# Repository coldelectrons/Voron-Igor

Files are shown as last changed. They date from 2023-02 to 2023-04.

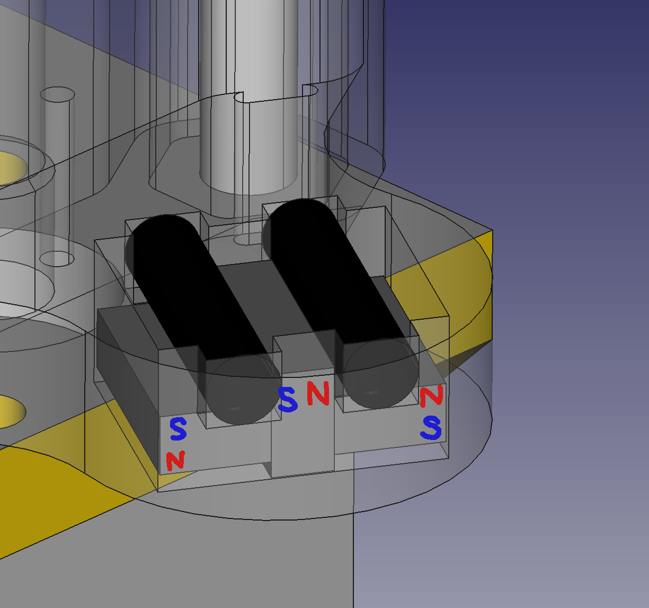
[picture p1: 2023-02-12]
pics/magnets_halbach_z_carriage.png

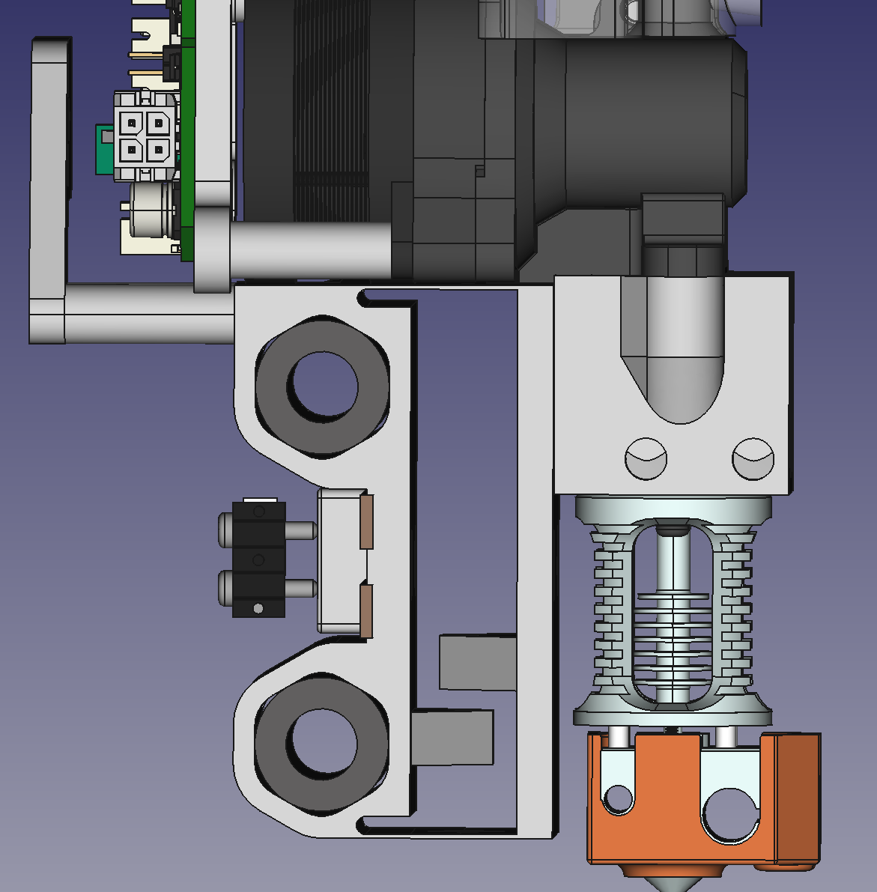
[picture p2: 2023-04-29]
pics/voron-igor-unklicky-tap-flexure.png

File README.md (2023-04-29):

# Voron Igor
It's a few good printers.

## What this is
This is my mods for a Voron Legacy.

## What did I mod?
Oh, not much.

### The tensioning idlers and motor mounts
It seems silly to come up with a good implementation and not use it simply because you
want to 'harken back' to the bad ol' days.

I have always disliked designs that tension the belts by moving the motor - and needing to
loosen/tighten 2 or more screws, relying on the motor to slide smoothly against a printed surface,
and/or needing to reach hard-to-reach places to adjust.  So I adapted the tension idlers from
the V2.4, and the motor mounts as well.

### The Y rod mounts
I elected to use some OpenBuilds 2020 extrusion I had, so it probably wasn't perfect, and the slots
were different...but the difference highlighted a design flaw in the original Legacy: The Y rods
get supported by two different datums at each end.

In the back, there is a single part that is located by the 2020 slot, and the rod spacing is fixed, and
as accurate and repeatable as the printer used to print that part.

In the front, the original idlers were a sandwich on the top and bottom of the 2020, and used pockets
to hold the rods.  Any variation the in the 2020 would mean that those rods could be not parallel.

So, I simply made a new Y rod support (x4), into which I also made a small cut so that when turned
the right direction, would allow the full travel of the gantry.

This also means that I could remove the idler tensioners, if need be, without unmounting the gantry.

### The Z axis
I found the original Legazy Z to be very...problematic. 

The rods were spaced far apart, which seemed to make rocking and binding of the whole thing to be too easy.

On top of rocking, it needed manual adjusting of the buildplate with screws. Which were on a wobbly Z axis.
That you had to touch.

This isn't 'harkening back', this is regressing.

So I adapted something like the Jubilee. I didn't know about the Voron Trident at the time, so that's what I was looking off of.

I didn't like the Jubilee's use of springs to hold down the kinematic table, because I could easily see myself
trying to lift a magnetic build plate off and stretching the springs. The springs Jubilee used were also tiny fiddly little bits.
So I came up with a solution to use magnets as effectively as possible, given what I had and could easily model.
The result is something that uses cheap magnets, in something like a Halbach array. The downside is that while I do have alot more
magnetic 'stick' than otherwise, the magnets I used are cheap, and so it's not enough to keep the table in place when I invert
the printer or turn it on it's side :)

### UnKlicky Tap?
I wanted to try making a Tap upgrade for a printer.

I'd already tried doing the KlickyNG probe, and got it working with the 'Z Calibration' hardware and Klipper module,
in order to hopefully work with any build plate I might want.

I can't say I liked it. Too much to configure, and too much that could go wrong. Naturally, when I saw the Voron Tap,
I realized I wanted something that simple - just touch the damn nozzle to the surface. Simple, right?

Right?

Because the Igor is using 8mm rods, it's not exactly stiff. Mass is a problem (always is on all printers),
and adding more wasn't an option. I also didn't want to have to source more special parts for my Igor.

I also have been wanting to try compliant mechanisms ('flexures') for a while.

Thus is born an X carriage with a flexure and a UnKlicky-esque probe switch.

Does it work? As of 20230429, I have successfully tested it for homing and probing.

## FAQ
### Why isn't this perfect
Partly because I was working on this through a couple upversions of FreeCAD, partly because I was learning more advanced
CAD as I went along, and partly because if there is one negative thing I might accuse the Voron designers of, it's CAD-wanking.

Sure, their designs work well, *and* they have a nice aesthetic, but when working from the STEP models, some things I had to
just take dimesions and start over, because of curved surfaces and such didn't let me easily mod things, or the imported STEP
would develop problems in FreeCAD when I tried to alter them.

### Why not include the full CAD files?
* My CAD files are a mess. I import other stuff, and the resulting file is HUGE.
* I use the FreeCAD-realthunder snap.
* If you open them in another FreeCAD version, they will likely break, or need a 'recompute now', at which time they will break.
* STEP files are stable

### Why the name 'Igor'?
Some people joking online saying the Legacy should have been named 'Frankenstein'
because they built it out of leftover parts. This is wrong, because Frankenstein was
the name of the *doctor*, not his creation.

I think it would be far more appropriate to adopt the name of a character from
Terry Pratchett's *Discworld* series:
 * the approach to self-improvement
 * the extreme recycling/upcycling
 * the spirit of Reprap in which one Igor can make many more
 * the way it is always just behind me when I need it

Alternative names I considered:
 * That Thing In the Cellar
 * Box O' Parts
 * Reprap Centipede

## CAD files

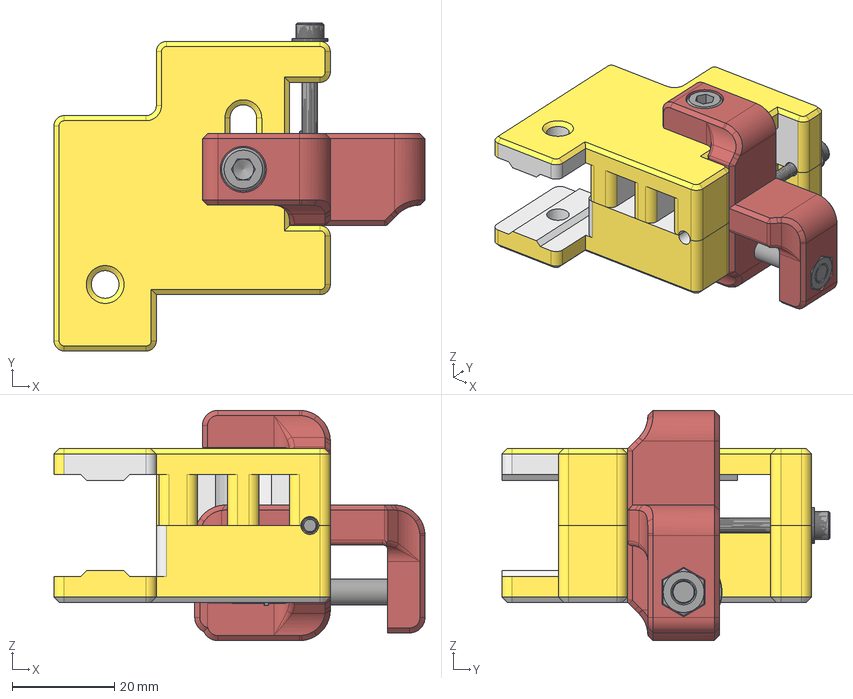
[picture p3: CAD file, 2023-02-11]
CAD/idler_A_assembly.step
72.5 x 64.1 x 45.0 mm
LCS_Origin x 6
M5x40 SHCS x 2
M5 1mm Spacer x 2
M3 Washer x 2
F695 ZZ x 2
M5 Hexnut x 2
M3 Threaded Insert (1) x 2
M3x40 SHCS x 2

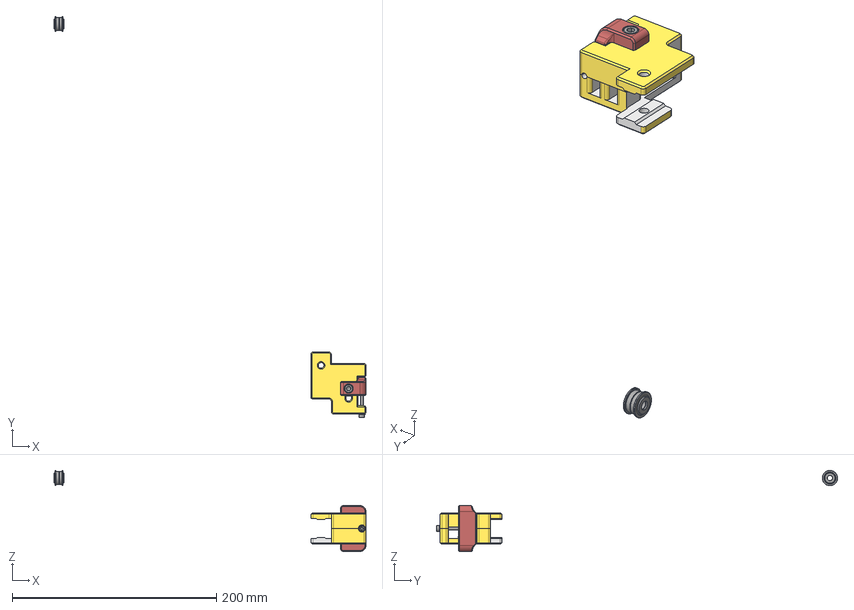
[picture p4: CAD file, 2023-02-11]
CAD/idler_B_assembly.step
305.6 x 392.9 x 79.5 mm
LCS_Origin x 6
M5x40 SHCS (1) x 2
F695 ZZ x 6
M5 1mm Spacer x 6
M5 Hexnut (1) x 2
M3x40 SHCS (1) x 2
M3 Washer x 2
M3 Threaded Insert (1) x 2

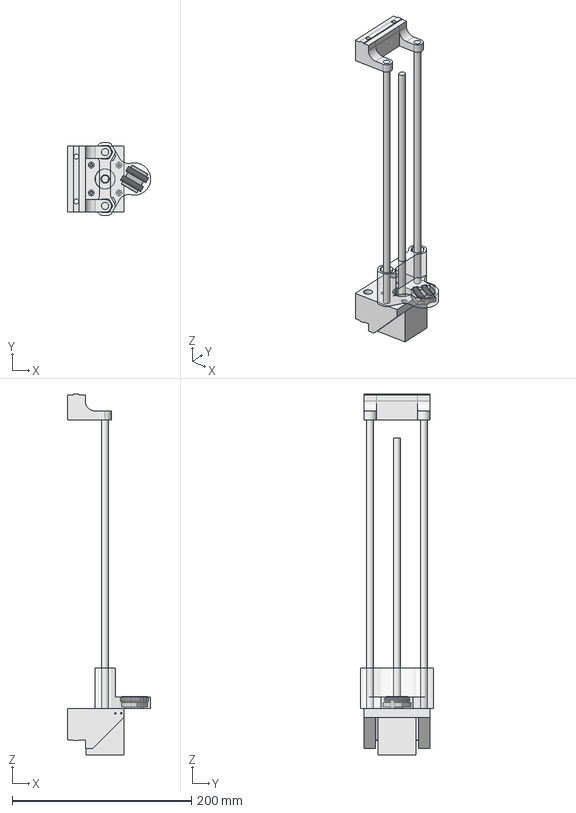
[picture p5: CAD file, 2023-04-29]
CAD/VL_configurable_z_unit.FCStd
93.0 x 81.0 x 403.0 mm
base
top
nema17_motor
leadscrew
rod1
rod2
carriage
dowels
magnets

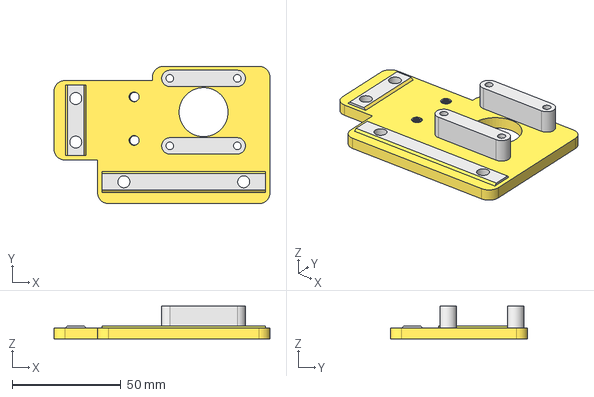
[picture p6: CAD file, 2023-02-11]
CAD/motor_A_bottom.step
99.2 x 63.0 x 15.0 mm
LCS_0003 x 2

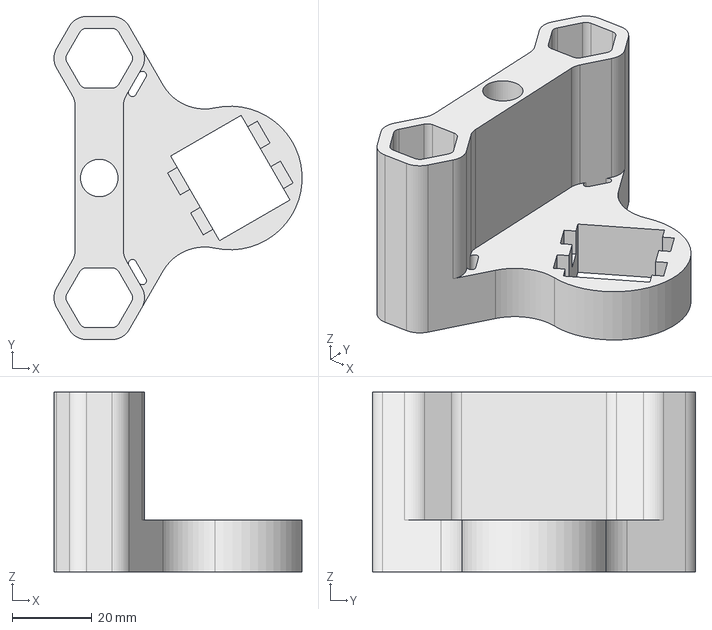
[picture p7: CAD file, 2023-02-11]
CAD/z_carriage_B.step
62.2 x 81.0 x 45.0 mm

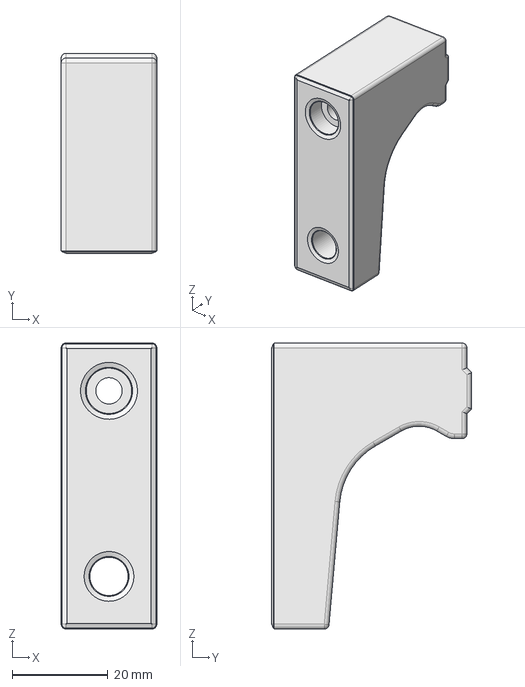
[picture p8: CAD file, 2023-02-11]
CAD/z_upper.step
20.0 x 41.9 x 59.8 mm

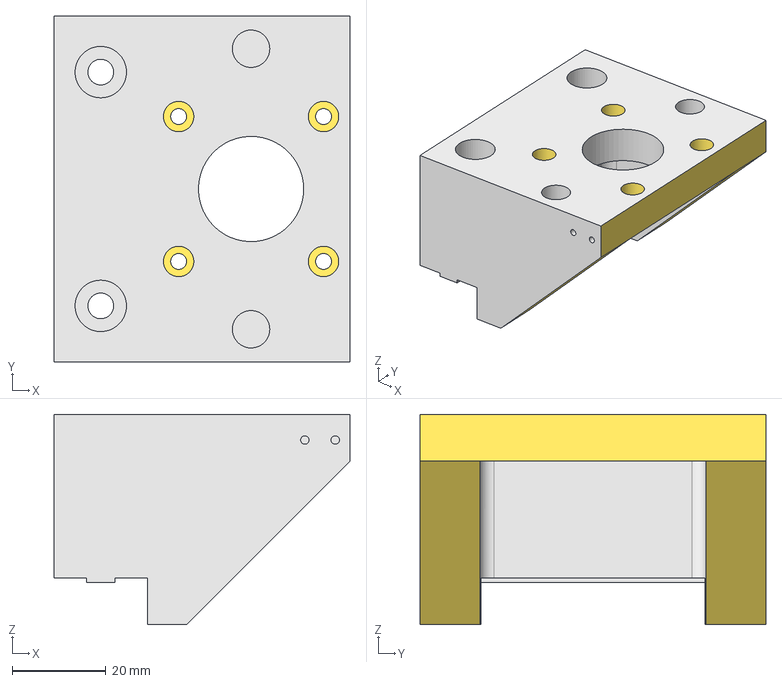
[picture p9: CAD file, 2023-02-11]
CAD/z_base.step
63.3 x 74.0 x 45.0 mm

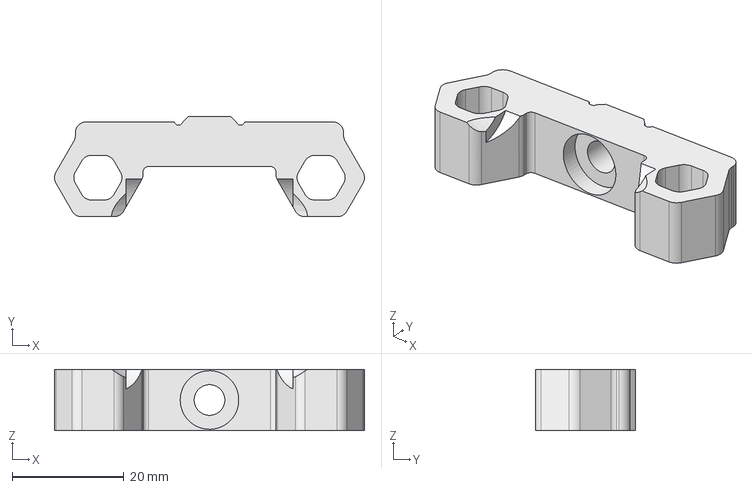
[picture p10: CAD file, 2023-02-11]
CAD/y_rod_mount.step
55.5 x 18.0 x 11.0 mm

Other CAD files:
CAD/motor_B_botton.step
CAD/motor_A_top.step
CAD/motor_B_top.step
CAD/z_carriage_back.step
CAD/z_carriage_A.step

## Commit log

2023-02-11 include x carriage parts
    [x_carriage_flexure.step, x_carriage_left.step, x_carriage_right.step]
2023-02-12 added initial pics and z axis freecad file
    [VL_configurable_z_unit.FCStd]
2023-04-29 second iteration of flexure, rebuilt entire head
    [VL_configurable_z_unit.FCStd, x_carriage_flexure.step, x_carriage_left.step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]
